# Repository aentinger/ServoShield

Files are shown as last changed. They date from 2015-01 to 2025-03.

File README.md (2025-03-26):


💾 Servo Shield
===============



# 📸 Image

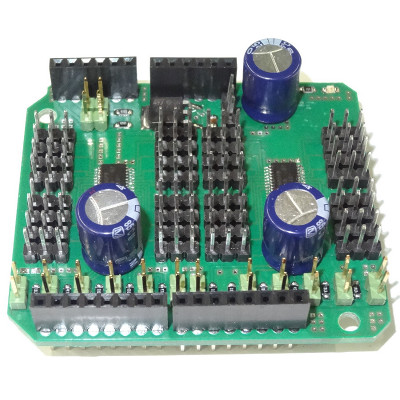
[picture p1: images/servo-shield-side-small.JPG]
LXRobotics P14 ServoShield


# 📂 Description

The LXRobotics Servo Shield facilitates the control of up to 32 model making (RC) servos. The control of the servos is done over two special ICs of type PCA9685 which communicates via I2C-Interface with Arduino - for the control of 32 servos only two Arduino Pins are required. For the servo supply, a dedicated linear voltage regulator is built on the Servo Shield, whereat using jumper can be switched over between the voltage regulator of the Servo Shield and the Arduino's power supply. Alternatively, the Servo Shield can be also externally power supplied via plug connector. For the quick start, a finished Arduino Library with sample programs is available.

**Features**

* Control of up to 32 Model making (RC) Servos
* Separate linear voltage regulator 
* Different options for the power supply of servos: Arduino, Servo Shield, Extern
* Control via I2C – thre are only two Arduino-Pins required (SDA, SCL)
* I2C-Address using Jumper adjustable - up to 25 = 32 different addresses possible
* Stackable - multiple Servo Shields can be put on top of each other and controlled over only one Arduino (theoretically 32 Servo Shields are possible)
* I2C-PullUp-Resistor via jumper adjustable
* Status-LED for the visualization of the supply state of the Servo Shields
* Activation/Deactivation of all Servo outputs of PCA 9685 over digital outputs possible ( function via jumper connected/disconnected)
* Arduino Library available for control with example programs

# 🎥 [Video](images/servo_shield_demo.mp4)

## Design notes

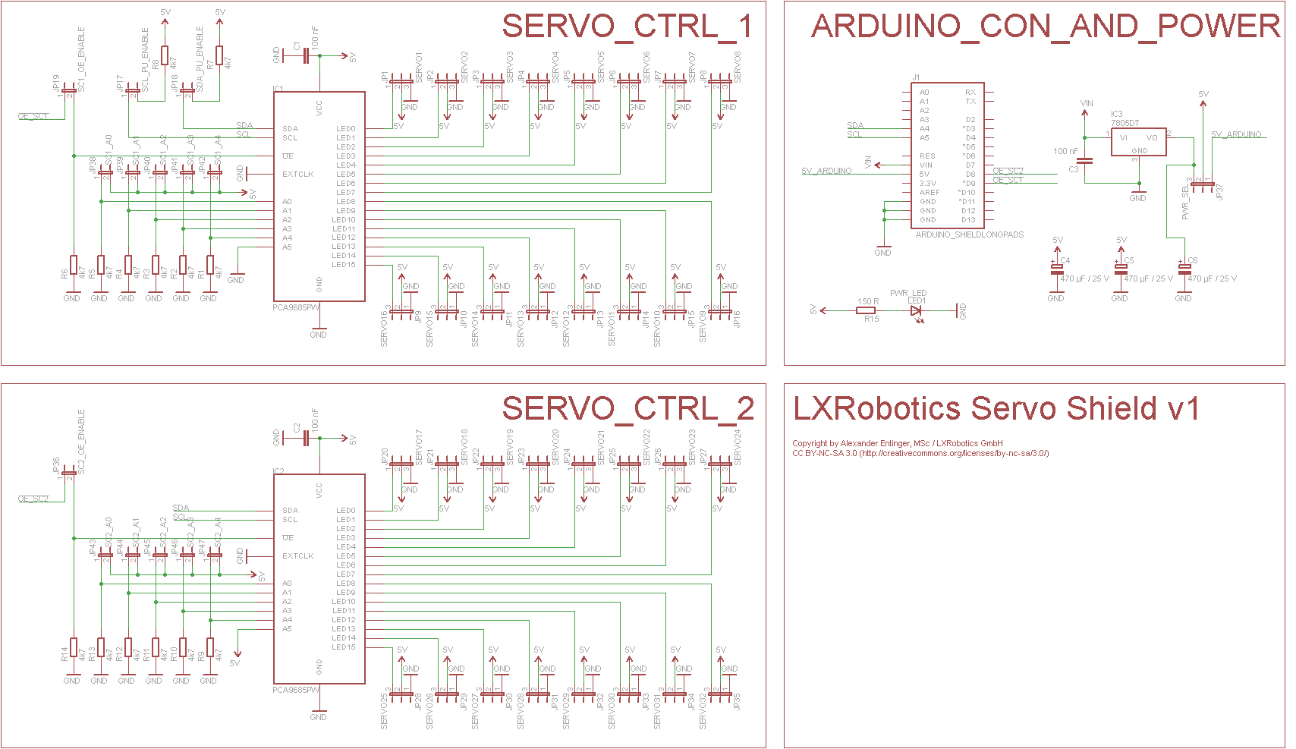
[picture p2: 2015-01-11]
hardware/lxr_servo_shield_v1.png

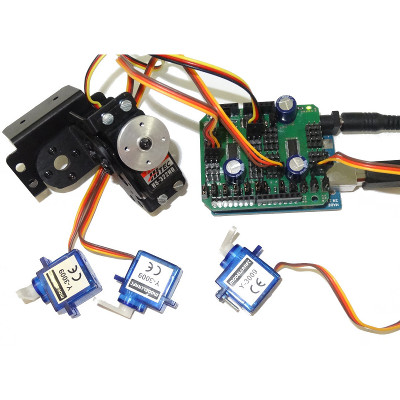
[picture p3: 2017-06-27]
images/servo-shield-action-small.JPG

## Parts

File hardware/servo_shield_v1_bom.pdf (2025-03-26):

Menge | Schaltplan | Bezeichnung | Farnell Bestell Nummer | Preis (1 Stück) | Gesamtpreis | Wird bestückt | Footprint | Säckchen
2 | IC1,IC2 | PCA9685PW I2C Servo-PWM-IC | 1854074 | € 1,92 | € 3,84 | x
33 | JP1-JP16,JP20-JP35,JP37 | Stiftleiste, 3-Polig, 2.54 mm | 1022249 | € 0,19 | € 6,27 | | | S1
14 | R1-R14 | 4k7, 0805, Widerstand SMD | 1469923 | € 0,02 | € 0,28 | x
14 | JP17-JP19,JP36,JP38-JP47 | Stiftleiste, 1 x 2, 2.54 mm, Vertikal, Durchsteck | 3418285 | € 0,24 | € 3,36 | | | S1
15 | | Jumper, 2.54 mm, 2 Polig | 4218176 | € 0,14 | € 2,04 | | | S1
3 | C1,C2,C3 | Kondensator, 100 nF, 16 V, 0805 | 1759144 | € 0,01 | € 0,03 | x
3 | C4,C5,C6 | 470 µF, 25 V, Elko, Radial | 1848502 | € 0,37 | € 1,11 | | | S2
1 | IC3 | LF50AB, 5 V LDO Regler, 1 A, SOT252 | 2296041 | € 1,02 | € 1,02 | x
1 | R15 | 150R, 0805, Widerstand SMD | 9333916 | € 0,01 | € 0,01 | x
1 | LED1 | SMD-LED, Grün, 0805, If=20 mA, Uf=2.1 | 1519498 | € 0,24 | € 0,24 | x
1 | J1 | Satz Arduino Buchsenleisten | ELV | € | 0,75 | € | 0,75 | S1 | http://www.elv.at/buchsenleisten-set-fuer-arduino-boards.html
| | | | Summe | | € | 18,95

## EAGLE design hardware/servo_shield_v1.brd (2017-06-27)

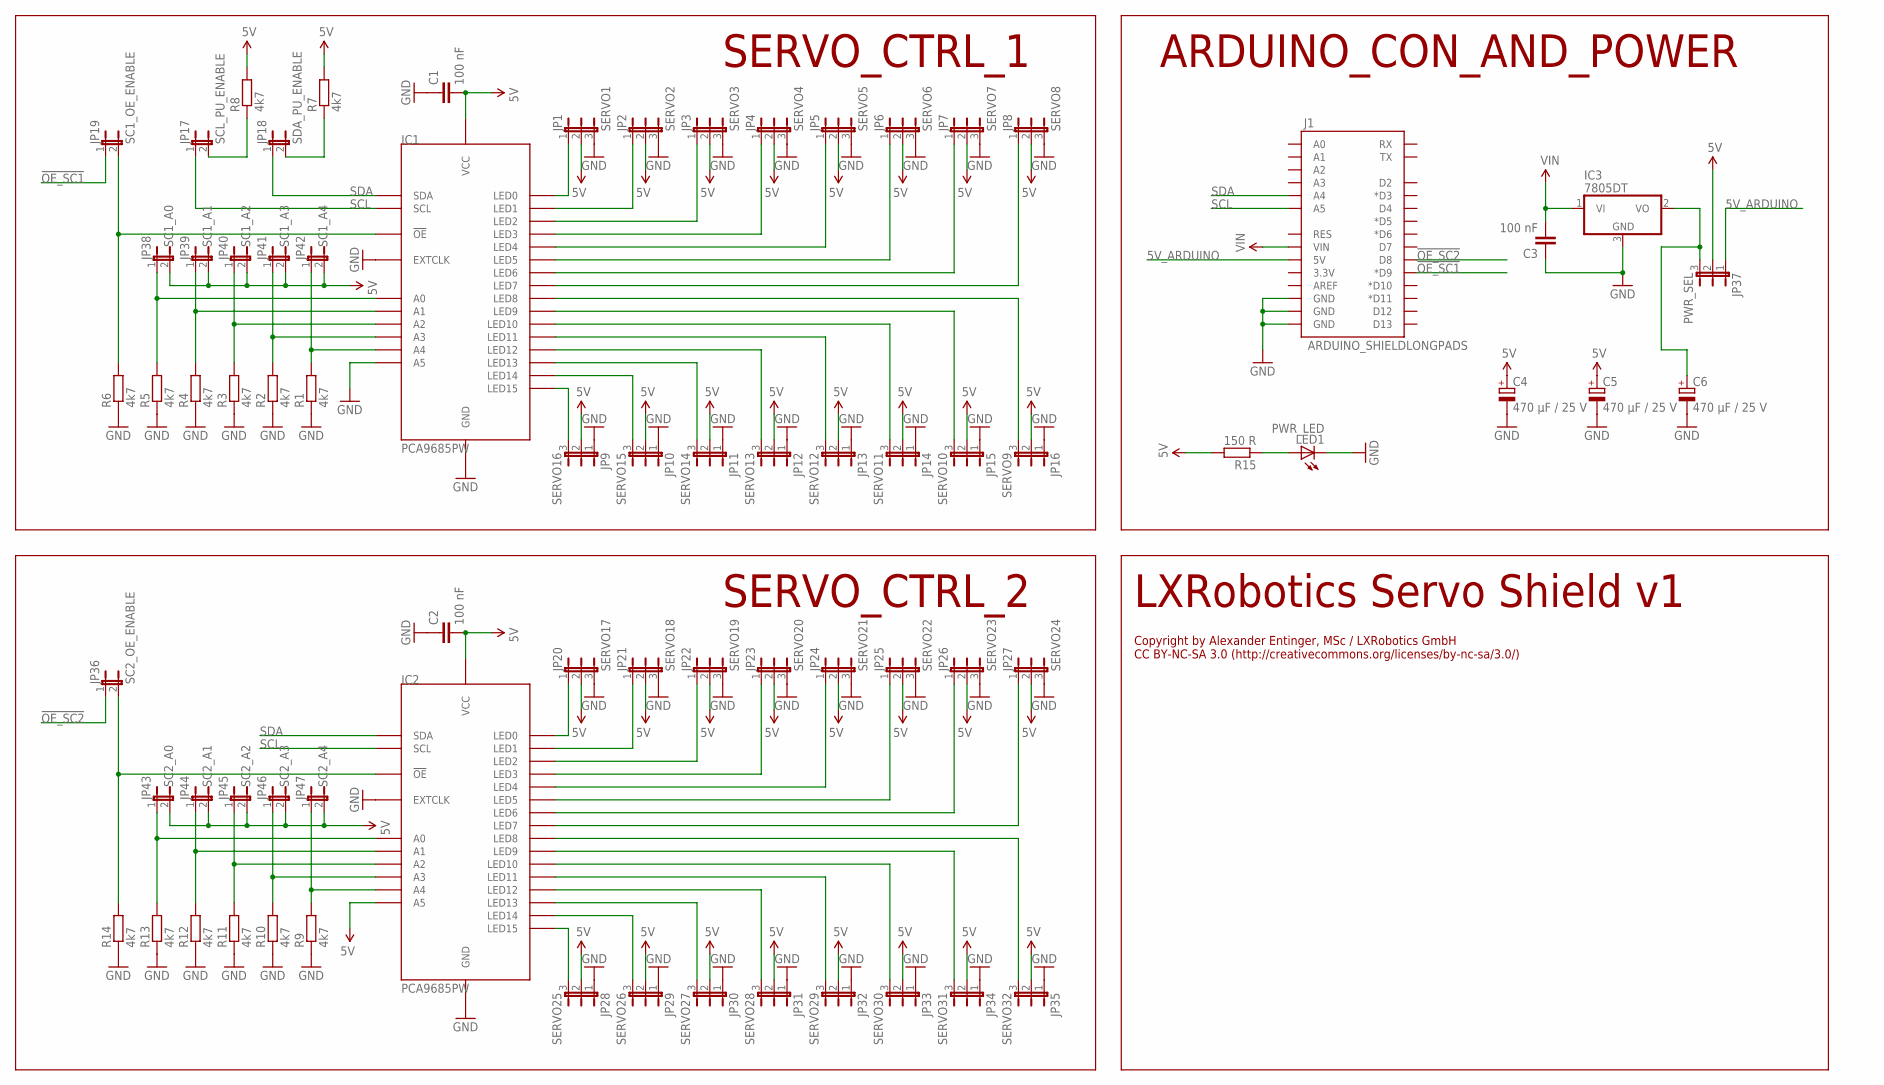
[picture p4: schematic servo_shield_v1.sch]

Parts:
C1, C2, C3: 100 nF; C0805K
C4, C5, C6: 470 µF / 25 V; E5-10,5
IC1, IC2: PCA9685PW; TSSOP28
IC3: 7805DT; TO252
J1: ARDUINO_SHIELDLONGPADS; DUEMILANOVE_SHIELD_LONGPADS
JP1: SERVO1; JP2
JP2: SERVO2; JP2
JP3: SERVO3; JP2
JP4: SERVO4; JP2
JP5: SERVO5; JP2
JP6: SERVO6; JP2
JP7: SERVO7; JP2
JP8: SERVO8; JP2
JP9: SERVO16; JP2
JP10: SERVO15; JP2
JP11: SERVO14; JP2
JP12: SERVO13; JP2
JP13: SERVO12; JP2
JP14: SERVO11; JP2
JP15: SERVO10; JP2
JP16: SERVO9; JP2
JP17: SCL_PU_ENABLE; JP1
JP18: SDA_PU_ENABLE; JP1
JP19: SC1_OE_ENABLE; JP1
JP20: SERVO17; JP2
JP21: SERVO18; JP2
JP22: SERVO19; JP2
JP23: SERVO20; JP2
JP24: SERVO21; JP2
JP25: SERVO22; JP2
JP26: SERVO23; JP2
JP27: SERVO24; JP2
JP28: SERVO25; JP2
JP29: SERVO26; JP2
JP30: SERVO27; JP2
JP31: SERVO28; JP2
JP32: SERVO29; JP2
JP33: SERVO30; JP2
JP34: SERVO31; JP2
JP35: SERVO32; JP2
JP36: SC2_OE_ENABLE; JP1
JP37: PWR_SEL; JP2
JP38: SC1_A0; JP1
JP39: SC1_A1; JP1
JP40: SC1_A2; JP1
JP41: SC1_A3; JP1
JP42: SC1_A4; JP1
JP43: SC2_A0; JP1
JP44: SC2_A1; JP1
JP45: SC2_A2; JP1
JP46: SC2_A3; JP1
JP47: SC2_A4; JP1
LED1: PWR_LED; CHIPLED_0805
R1, R2, R3, R4, R5, R6, R7, R8, R9, R10, R11, R12, R13, R14: 4k7; R0805W
R15: 150 R; R0805W

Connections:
5V: C1.2, C2.2, C4.+, C5.+, IC1.28 (VCC), IC2.24 (A5), IC2.28 (VCC), JP1.2, JP2.2, JP3.2, JP4.2, JP5.2, JP6.2, JP7.2, JP8.2, JP9.2, JP10.2, JP11.2, JP12.2, JP13.2, JP14.2, JP15.2, JP16.2, JP20.2, JP21.2, JP22.2, JP23.2, JP24.2, JP25.2, JP26.2, JP27.2, JP28.2, JP29.2, JP30.2, JP31.2, JP32.2, JP33.2, JP34.2, JP35.2, JP37.2, JP38.2, JP39.2, JP40.2, JP41.2, JP42.2, JP43.2, JP44.2, JP45.2, JP46.2, JP47.2, R7.2, R8.2, R15.2
5V_ARDUINO: J1.5V, JP37.1
!OE_SC1: J1.D9 (*D9), JP19.1
!OE_SC2: J1.D8, JP36.1
GND: C1.1, C2.1, C3.1, C4.-, C5.-, C6.-, IC1.14 (GND), IC1.24 (A5), IC1.25 (EXTCLK), IC2.14 (GND), IC2.25 (EXTCLK), IC3.3 (GND), J1.GND@0 (GND), J1.GND@1 (GND), J1.GND@2 (GND), JP1.3, JP2.3, JP3.3, JP4.3, JP5.3, JP6.3, JP7.3, JP8.3, JP9.1, JP10.1, JP11.1, JP12.1, JP13.1, JP14.1, JP15.1, JP16.1, JP20.3, JP21.3, JP22.3, JP23.3, JP24.3, JP25.3, JP26.3, JP27.3, JP28.1, JP29.1, JP30.1, JP31.1, JP32.1, JP33.1, JP34.1, JP35.1, LED1.C, R1.1, R2.1, R3.1, R4.1, R5.1, R6.1, R9.1, R10.1, R11.1, R12.1, R13.1, R14.1
unnamed: IC1.6 (LED0), JP1.1
unnamed: IC1.7 (LED1), JP2.1
unnamed: IC1.8 (LED2), JP3.1
unnamed: IC1.9 (LED3), JP4.1
unnamed: IC1.10 (LED4), JP5.1
unnamed: IC1.11 (LED5), JP6.1
unnamed: IC1.12 (LED6), JP7.1
unnamed: IC1.13 (LED7), JP8.1
unnamed: IC1.22 (LED15), JP9.3
unnamed: IC1.21 (LED14), JP10.3
unnamed: IC1.20 (LED13), JP11.3
unnamed: IC1.19 (LED12), JP12.3
unnamed: IC1.18 (LED11), JP13.3
unnamed: IC1.17 (LED10), JP14.3
unnamed: IC1.16 (LED9), JP15.3
unnamed: IC1.15 (LED8), JP16.3
unnamed: IC1.5 (A4), JP42.1, R1.2
unnamed: IC1.4 (A3), JP41.1, R2.2
unnamed: IC1.3 (A2), JP40.1, R3.2
unnamed: IC1.2 (A1), JP39.1, R4.2
unnamed: IC1.1 (A0), JP38.1, R5.2
unnamed: IC1.23 (!OE), JP19.2, R6.2
unnamed: C6.+, IC3.2 (VO), JP37.3
unnamed: IC2.6 (LED0), JP20.1
unnamed: IC2.7 (LED1), JP21.1
unnamed: JP17.2, R8.1
unnamed: JP18.2, R7.1
unnamed: IC2.8 (LED2), JP22.1
unnamed: IC2.9 (LED3), JP23.1
unnamed: IC2.10 (LED4), JP24.1
unnamed: IC2.11 (LED5), JP25.1
unnamed: IC2.12 (LED6), JP26.1
unnamed: IC2.13 (LED7), JP27.1
unnamed: IC2.22 (LED15), JP28.3
unnamed: IC2.21 (LED14), JP29.3
unnamed: IC2.20 (LED13), JP30.3
unnamed: IC2.19 (LED12), JP31.3
unnamed: IC2.18 (LED11), JP32.3
unnamed: IC2.17 (LED10), JP33.3
unnamed: IC2.16 (LED9), JP34.3
unnamed: IC2.15 (LED8), JP35.3
unnamed: IC2.5 (A4), JP47.1, R9.2
unnamed: IC2.4 (A3), JP46.1, R10.2
unnamed: IC2.3 (A2), JP45.1, R11.2
unnamed: IC2.2 (A1), JP44.1, R12.2
unnamed: IC2.1 (A0), JP43.1, R13.2
unnamed: IC2.23 (!OE), JP36.2, R14.2
unnamed: LED1.A, R15.1
SCL: IC1.26 (SCL), IC2.26 (SCL), J1.A5, JP17.1
SDA: IC1.27 (SDA), IC2.27 (SDA), J1.A4, JP18.1
VIN: C3.2, IC3.1 (VI), J1.VIN

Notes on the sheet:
SERVO_CTRL_1
SERVO_CTRL_2
ARDUINO_CON_AND_POWER
LXRobotics Servo Shield v1
Copyright by Alexander Entinger, MSc / LXRobotics GmbH CC BY-NC-SA 3.0 (http://creativecommons.org/licenses/by-nc-sa/3.0/)

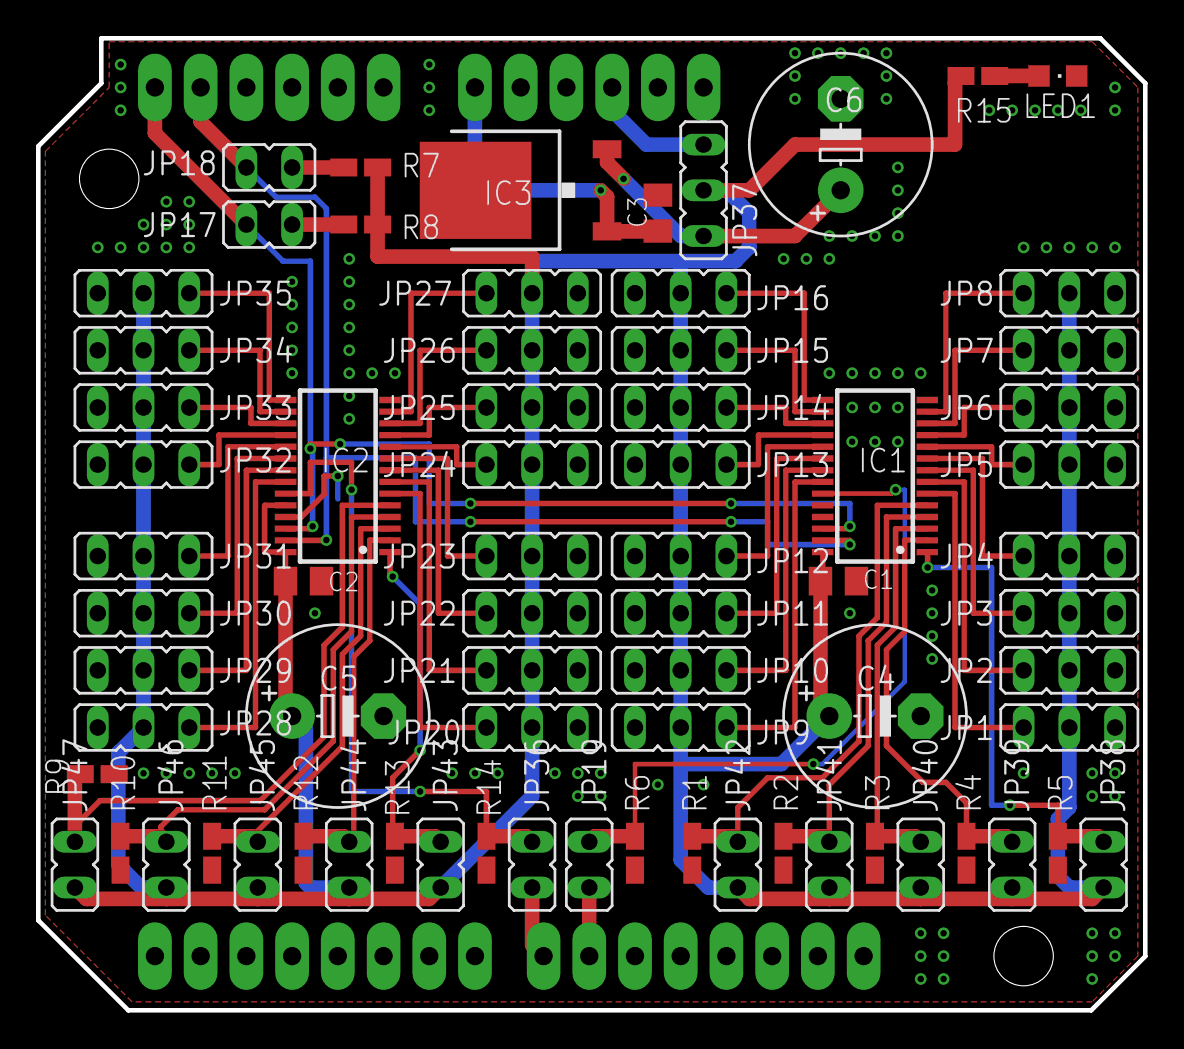
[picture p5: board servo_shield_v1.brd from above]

Board: 2 copper layers, 61.5 x 54.0 mm, 73 parts (0 on the bottom side), 56 nets.

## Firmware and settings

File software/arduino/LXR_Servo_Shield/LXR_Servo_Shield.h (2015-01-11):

/**
 * @author Alexander Entinger, MSc / LXRobotics
 * @brief this module implements the library for controlling the LXRobotics Servo Shield for controlling up to 32 servos
 * @file LXR_Servo_Shield.h
 * @license Attribution-NonCommercial-ShareAlike 3.0 Unported (CC BY-NC-SA 3.0) ( http://creativecommons.org/licenses/by-nc-sa/3.0/ )
 */

#ifndef LXR_SERVO_SHIELD_H_
#define LXR_SERVO_SHIELD_H_

/* INCLUDES */
 
#include "Arduino.h"

/* DEFINES */

//#define _DEBUG_ENABLED

#define REG_LED_0           (0x08)  // LED0_OFF_L
#define REG_LED_1           (REG_LED_0+1*4)
#define REG_LED_2           (REG_LED_0+2*4)
#define REG_LED_3           (REG_LED_0+3*4)
#define REG_LED_4           (REG_LED_0+4*4)
#define REG_LED_5           (REG_LED_0+5*4)
#define REG_LED_6           (REG_LED_0+6*4)
#define REG_LED_7           (REG_LED_0+7*4)
#define REG_LED_8           (REG_LED_0+8*4)
#define REG_LED_9           (REG_LED_0+9*4)
#define REG_LED_10          (REG_LED_0+10*4)
#define REG_LED_11          (REG_LED_0+11*4)
#define REG_LED_12          (REG_LED_0+12*4)
#define REG_LED_13          (REG_LED_0+13*4)
#define REG_LED_14          (REG_LED_0+14*4)
#define REG_LED_15          (REG_LED_0+15*4)

/* GLOBAL CONSTANTS */

// NO JUMPERS SET
static byte const IC1_DEV_ADDR_NO_JUMPERS_SET = 0x40;
static byte const IC2_DEV_ADDR_NO_JUMPERS_SET = 0x60;
// ALL JUMPERS SET
static byte const IC1_DEV_ADDR_ALL_JUMPERS_SET = 0x5F;
static byte const IC2_DEV_ADDR_ALL_JUMPERS_SET = 0x7F;
// and there are 32 other combinations possibble ... (depending on how the address jumpers are set)

/* TYPEDEFS */

typedef enum
{
   SERVO_1 = 0,
   SERVO_2 = 1,
   SERVO_3 = 2,
   SERVO_4 = 3,
   SERVO_5 = 4,
   SERVO_6 = 5,
   SERVO_7 = 6,
   SERVO_8 = 7,
   SERVO_9 = 8,
   SERVO_10 = 9,
   SERVO_11 = 10,
   SERVO_12 = 11,
   SERVO_13 = 12,
   SERVO_14 = 13,
   SERVO_15 = 14,
   SERVO_16 = 15,
   SERVO_17 = 16,
   SERVO_18 = 17,
   SERVO_19 = 18,
   SERVO_20 = 19,
   SERVO_21 = 20,
   SERVO_22 = 21,
   SERVO_23 = 22,
   SERVO_24 = 23,
   SERVO_25 = 24,
   SERVO_26 = 25,
   SERVO_27 = 26,
   SERVO_28 = 27,
   SERVO_29 = 28,
   SERVO_30 = 29,
   SERVO_31 = 30,
   SERVO_32 = 31
} E_SERVO_SELECT;

typedef enum {IC1 = 0, IC2 = 1} E_IC_SELECT;

/* PROTOTYPES */

class LXR_Servo_Shield 
{
public:
  /**
   * @brief Constructor
   * @param ic_1_dev_address i2c address of the pwm ic1 (selectable by jumpers)
   * @param ic_2_dev_address i2c address of the pwm ic2 (selectable by jumpers)
   * @param use_oe_enable_pins make use of the output enable pins
   */
  LXR_Servo_Shield(byte const ic_1_dev_addr, byte const ic_2_dev_addr, boolean const use_oe_enable_pins);
  
  /**
   * @brief initializes the servo shield
   */
  void begin();
  
  /** 
   * @brief sets the pins OE_SC1 and OE_SC2 to LOW, therefor the pwm outputs of all servos are enabled
   * @return true in case of success, false in case of failure (use_oe_enable_pins in ctor must be set to true + jumpers SC1_OE_ENABLE and SC2_OE_ENABLE) must be set)
   */
  boolean enable_pwm_outputs();

  /** 
   * @brief sets the pins OE_SC1 and OE_SC2 to HIGH, therefor the pwm outputs of all servos are disabled
   * @return true in case of success, false in case of failure (use_oe_enable_pins in ctor must be set to true + jumpers SC1_OE_ENABLE and SC2_OE_ENABLE) must be set)
   */  
  boolean disable_pwm_outputs();
  
  /** 
   * @brief sets the servo output selected by sel to have a pulse with pulse_duration_us microseconds - ATTENTION: BE CAREFUL THAT THE SET PULSE DURATION IS WITHIN THE SERVO SPECIFICATION of 1000 to 2000 us - OPERATING YOUR SERVO OUTIDE OF THIS SPECIFICATION CAN DESTROY OR DAMAGE YOUR SERVO !
   */
  void set_servo_pulse_duration(E_SERVO_SELECT const sel, int const pulse_duration_us);
  
private:
  boolean const m_use_oe_enable_pins;
  byte m_ic_dev_addr[2];
   
#ifdef _DEBUG_ENABLED  
  /** 
   * @brief read a byte from one of the two pwm ics (reg describes the reg address)
   */
  byte read_byte(E_IC_SELECT const sel, byte const reg);
#endif
  
  /** 
   * @brief writes a byte to one of the two pwm ics (reg describes the reg address)
   */
  void write_byte(E_IC_SELECT const sel, byte const reg, byte const data);
  
  /**
   * @brief set the servo pwm value
   */
  void set_servo_pwm(E_IC_SELECT const ic_sel, byte const led_reg, int const pulse_duration_us);
};

#endif

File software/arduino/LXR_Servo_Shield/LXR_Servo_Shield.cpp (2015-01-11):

/**
 * @author Alexander Entinger, MSc / LXRobotics
 * @brief this module implements the library for controlling the LXRobotics Servo Shield for controlling up to 32 servos
 * @file LXR_Servo_Shield.cpp
 * @license Attribution-NonCommercial-ShareAlike 3.0 Unported (CC BY-NC-SA 3.0) ( http://creativecommons.org/licenses/by-nc-sa/3.0/ )
 */
 
/* INCLUDES */

#include "LXR_Servo_Shield.h"
#include "Wire.h"

/* DEFINES */

// REG ADDRESSES
#define REG_MODE1           (0x00)
#define REG_PRE_SCALE       (0xFE)

// BITMAPS
#define MODE1_AI_bm         (1<<5)
#define MODE1_SLEEP_bm      (1<<4)
#define MODE1_ALLCALL_bm    (1<<0)

/* TYPEDEFS */

typedef struct
{
  E_IC_SELECT ic_sel;
  byte led_reg;
} s_servo_map;
  

/* GLOBAL CONSTANTS */

static int const OE_SC1_PIN = 9; // D9
static int const OE_SC2_PIN = 8; // D8
  
static s_servo_map const m_servo_map[] =
{
  {IC1, REG_LED_0}, // SERVO_1
  {IC1, REG_LED_1}, // SERVO_2
  {IC1, REG_LED_2}, // SERVO_3
  {IC1, REG_LED_3}, // SERVO_4
  {IC1, REG_LED_4}, // SERVO_5
  {IC1, REG_LED_5}, // SERVO_6
  {IC1, REG_LED_6}, // SERVO_7
  {IC1, REG_LED_7}, // SERVO_8
  {IC1, REG_LED_8}, // SERVO_9
  {IC1, REG_LED_9}, // SERVO_10
  {IC1, REG_LED_10}, // SERVO_11
  {IC1, REG_LED_11}, // SERVO_12
  {IC1, REG_LED_12}, // SERVO_13
  {IC1, REG_LED_13}, // SERVO_14
  {IC1, REG_LED_14}, // SERVO_15
  {IC1, REG_LED_15}, // SERVO_16
  {IC2, REG_LED_0}, // SERVO_17
  {IC2, REG_LED_1}, // SERVO_18
  {IC2, REG_LED_2}, // SERVO_19
  {IC2, REG_LED_3}, // SERVO_20
  {IC2, REG_LED_4}, // SERVO_21
  {IC2, REG_LED_5}, // SERVO_22
  {IC2, REG_LED_6}, // SERVO_23
  {IC2, REG_LED_7}, // SERVO_24
  {IC2, REG_LED_8}, // SERVO_25
  {IC2, REG_LED_9}, // SERVO_26
  {IC2, REG_LED_10}, // SERVO_27
  {IC2, REG_LED_11}, // SERVO_28
  {IC2, REG_LED_12}, // SERVO_29
  {IC2, REG_LED_13}, // SERVO_30
  {IC2, REG_LED_14}, // SERVO_31
  {IC2, REG_LED_15} // SERVO_32
};

/* FUNCTIONS */

/**
 * @brief Constructor initializes the servo shield
 * @param ic_1_dev_address i2c address of the pwm ic1 (selectable by jumpers)
 * @param ic_2_dev_address i2c address of the pwm ic2 (selectable by jumpers)
 * @param use_oe_enable_pins make use of the output enable pins
 */
LXR_Servo_Shield::LXR_Servo_Shield(byte const ic_1_dev_addr, byte const ic_2_dev_addr, boolean const use_oe_enable_pins) : m_use_oe_enable_pins(use_oe_enable_pins)
{
  // assign i2c addresses
  m_ic_dev_addr[IC1] = ic_1_dev_addr;
  m_ic_dev_addr[IC2] = ic_2_dev_addr;
}

/**
 * @brief initializes the servo shield
 */
void LXR_Servo_Shield::begin()
{
  // initialize wire library
  Wire.begin();
  // setup oe enable pins
  if(m_use_oe_enable_pins)
  {
    pinMode(OE_SC1_PIN, OUTPUT);
    pinMode(OE_SC2_PIN, OUTPUT);
    disable_pwm_outputs();
  }
  // write default configuration to register MODE1
  write_byte(IC1, REG_MODE1, (MODE1_SLEEP_bm | MODE1_ALLCALL_bm));
  write_byte(IC2, REG_MODE1, (MODE1_SLEEP_bm | MODE1_ALLCALL_bm));
  // set pwm frequency = 50 Hz = 20 ms, prescale = round(25MHz/(4096*50)) - 1 = 121
  write_byte(IC1, REG_PRE_SCALE, 121);
  write_byte(IC2, REG_PRE_SCALE, 121);
  // deactivate sleep mode and activate auto increment mode
  write_byte(IC1, REG_MODE1, (MODE1_AI_bm | MODE1_ALLCALL_bm));
  write_byte(IC2, REG_MODE1, (MODE1_AI_bm | MODE1_ALLCALL_bm));  
  // wait a bit to get the oscillator up and running
  delay(100);
  
#ifdef _DEBUG_ENABLED
  // activate serial for debug purposes
  Serial.begin(115200);
  byte buf[32], length;
  length = sprintf((char*)(buf), "IC1.MODE1 = 0x%x\n", read_byte(IC1, REG_MODE1));
  Serial.write(buf, length);
  length = sprintf((char*)(buf), "IC2.MODE1 = 0x%x\n", read_byte(IC2, REG_MODE1));
  Serial.write(buf, length);
  length = sprintf((char*)(buf), "IC1.PRE_SCALE = 0x%x\n", read_byte(IC1, REG_PRE_SCALE));
  Serial.write(buf, length);
  length = sprintf((char*)(buf), "IC2.PRE_SCALE = 0x%x\n", read_byte(IC2, REG_PRE_SCALE));
  Serial.write(buf, length);
#endif  
}

/** 
 * @brief sets the pins OE_SC1 and OE_SC2 to LOW, therefor the pwm outputs of all servos are enabled
 * @return true in case of success, false in case of failure (use_oe_enable_pins in ctor must be set to true + jumpers SC1_OE_ENABLE and SC2_OE_ENABLE) must be set)
 */
boolean LXR_Servo_Shield::enable_pwm_outputs()
{
  if(m_use_oe_enable_pins)
  {
    digitalWrite(OE_SC1_PIN, LOW);
    digitalWrite(OE_SC2_PIN, LOW);
    return true;
  }
  else
  {
    return false;
  }
}

/** 
 * @brief sets the pins OE_SC1 and OE_SC2 to HIGH, therefor the pwm outputs of all servos are disabled
 * @return true in case of success, false in case of failure (use_oe_enable_pins in ctor must be set to true + jumpers SC1_OE_ENABLE and SC2_OE_ENABLE) must be set)
 */  
boolean LXR_Servo_Shield::disable_pwm_outputs()
{
  if(m_use_oe_enable_pins)
  {
    digitalWrite(OE_SC1_PIN, HIGH);
    digitalWrite(OE_SC2_PIN, HIGH);
    return true;
  }
  else
  {
    return false;
  }
}

/** 
 * @brief sets the servo output selected by sel to have a pulse with pulse_duration_us microseconds - ATTENTION: BE CAREFUL THAT THE SET PULSE DURATION IS WITHIN THE SERVO SPECIFICATION of 1000 to 2000 us - OPERATING YOUR SERVO OUTIDE OF THIS SPECIFICATION CAN DESTROY OR DAMAGE YOUR SERVO !
 */
void LXR_Servo_Shield::set_servo_pulse_duration(E_SERVO_SELECT const sel, int const pulse_duration_us)
{
  set_servo_pwm(m_servo_map[sel].ic_sel, m_servo_map[sel].led_reg, pulse_duration_us);
}

#ifdef _DEBUG_ENABLED  
/** 
 * @brief read a byte from one of the two pwm ics (reg describes the reg address)
 */
byte LXR_Servo_Shield::read_byte(E_IC_SELECT const sel, byte const reg)
{
  Wire.beginTransmission(m_ic_dev_addr[sel]);
  Wire.write(reg);
  Wire.endTransmission();

  Wire.requestFrom(m_ic_dev_addr[sel], (byte)(1));
  return Wire.read();
}
#endif

/** 
 * @brief writes a byte to one of the two pwm ics (reg describes the reg address)
 */
void LXR_Servo_Shield::write_byte(E_IC_SELECT const sel, byte const reg, byte const data)
{
  Wire.beginTransmission(m_ic_dev_addr[sel]);
  Wire.write(reg);
  Wire.write(data);
  Wire.endTransmission();
}

/**
 * @brief set the servo pwm value
 */
void LXR_Servo_Shield::set_servo_pwm(E_IC_SELECT const ic_sel, byte const led_reg, int const pulse_duration_us)
{
  // 20 ms / 4096 = 4.8828 us = 1 Timertick => 1 us = 1/4.883 Timerticks
  int const timer_ticks = min(((uint32_t)(pulse_duration_us) * 100) / 488, 4095);
    
  Wire.beginTransmission(m_ic_dev_addr[ic_sel]);
  Wire.write(led_reg);

  // write LEDx_OFF_L
  Wire.write((byte)(timer_ticks & 0xFF));
  // write LEDx_OFF_H
  Wire.write((byte)((timer_ticks >> 8) & 0xFF));

  Wire.endTransmission();
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

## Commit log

2015-01-11 initial checkin of servo shield software support pack
2017-06-27 Adding images + hardware
    [servo_shield_v1.brd, servo_shield_v1.sch]
2025-03-26 Upload servo shield demo.
2025-03-26 Adding BOM.

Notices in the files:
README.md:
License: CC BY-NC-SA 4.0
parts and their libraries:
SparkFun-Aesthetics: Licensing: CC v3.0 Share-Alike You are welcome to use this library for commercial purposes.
